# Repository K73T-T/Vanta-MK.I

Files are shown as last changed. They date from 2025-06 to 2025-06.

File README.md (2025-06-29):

# Vanta-MK.I
Vanta Mk.I is a custom, experimental 3D printer that uses a serial [SCARA](https://en.wikipedia.org/wiki/SCARA) arm for its motion system, instead of the more common Cartesian or CoreXY setups. It’s designed to explore uncommon 3D printing mechanics and share them through an open-source project.

# Project goals
- Capible of printing up to 600mm/s
- Print at 350mm/s reliably
- Easily serviceable
- full 24v electrical system
- V6 hotend
- Direct drive extruder
- Heated build plate
- Greater than 200x200x250 build volume
- stays togeter when tipped upside down

# Cad As of 6/26/25 



Onshape Document: https://cad.onshape.com/documents/15ec733589f1dfb19432007e/w/fc0f806dac7b21e964ade97e/e/b542b6b24f478e7f12932bdf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
440x440x722mm

|Hardware | | | | | |
|---|---|---|---|---|---|
| |PART |UNIT COST |QUANTITY|TOTAL |LINK |
| |150 Pieces M6 Screws Nuts Washers Set |$9.99 |1 |$9.99 |https://a.co/d/1KRJd6D |
| |GT2 Timing Belt Tensioner Torsion Spring |$1.63 |1 |$1.63 |https://www.aliexpress.us/item/2251832660949905.html? |
| |5 to 8 mm shaft coupling |$1.21 |2 |$2.42 |https://www.aliexpress.us/item/2251832618318567.html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 |
| |2m gt2 6mm width open loop belt |$5.54 |1 |$5.54 |https://www.aliexpress.us/item/3256805930504641.html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 |
| |Micro Limit Switch KW12-3 AC 250V 5A SPDT 1NO 1NC Micro Switch With Roller |$3.18 |1 |$3.18 |https://www.aliexpress.us/item/3256808277942672.html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 |
| |2040 extrusion 600mm |$0.00 |1 |$0.00 |Already owned |
| |2040 extrusion 400mm |$0.00 |1 |$0.00 |Already owned |
| |2020 extrusion 200mm |$0.00 |2 |$0.00 |Already owned |
| |2020 extrusion 180mm |$0.00 |6 |$0.00 |Already owned |
| |2020 extrusion 400mm |$0.00 |7 |$0.00 |Already owned |
| |2020 extrusion 550mm |$0.00 |4 |$0.00 |Already owned |
| |2020 extrusion 440mm |$0.00 |1 |$0.00 |Already owned |
| |2020 extrusion 360mm |$0.00 |4 |$0.00 |Already owned |
| |2PCS 350mm（13.78 Inches）Tr8x8 Lead Screw with T8 Brass Nut |$13.99 |1 |$13.99|https://a.co/d/b3srbob |
| |M3 countersunk screw set |$9.99 |1 |$9.99 |https://a.co/d/4OXnjIt |
| |Anycubic Kobra 3 Build plate assembly |$18.99 |1 |$18.99|https://a.co/d/51d8Cin |
| |m3 standoff set |$6.77 |1 |$6.77 |https://a.co/d/bvQ3HL7 |
| |24V 480W Switching Power Supply Adapter SMPS AC 110/220V to DC 24V |$30.99 |1 |$30.99|https://www.amazon.com/dp/B0CD1N3QH4?ref_=cm_sw_r_cp_ud_dp_ZGNP1G9RJW46EPHEQV2K_1 |
| |2Pcs 6mm x 400mm (0.236 x 15.74 inches) Vigorous Linear Motion Rods |$9.39 |2 |$18.78|https://a.co/d/gR9NUPh |
| |8Pcs LM6UU Linear Bearings |$8.81 |1 |$8.81 |https://a.co/d/9uNp9xQ |
| |2PCS Set GT2 Synchronous Wheel 20&36 Teeth 5mm Bore |$7.99 |1 |$7.99 |https://a.co/d/7NZQ2OG |
| |608zz ball bearing |$0.00 |7 |$0.00 |Already owned |
| |ruthex M3 Threaded Inserts Short - 100 Pieces RX-M3Sx4.0 Brass Heat Set Insert for Plastic Parts|$10.99 |1 |$10.99|https://a.co/d/din7U3K |
| |100x 304 Stainless Steel Balls 4mm |$2.60 |1 |$2.60 |https://www.aliexpress.us/item/3256808582039444.html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"order"%3A"104"%2C"eval"%3A"1"%7D&pdp_npi=4%40dis%21USD%211.89%211.79%21%21%211.89%211.79%21%402101c71a17490199564722814e3e99%2112000046585415385%21sea%21US%213447209169%21X&curPageLogUid=0d0BXeuBR6GZ&utparam-url=scene%3Asearch%7Cquery_from%3A&search_p4p_id=202506032352367638279615146210005463318_1 |
| |50x M3 x 30 Stainless Black 12.9 Grade Steel DIN912 Socket Cap Bolt |$4.17 |1 |$4.17 |https://www.aliexpress.us/item/3256802096694558.html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"order"%3A"159"%2C"eval"%3A"1"%7D&pdp_npi=4%40dis%21USD%213.34%213.14%21%21%213.34%213.14%21%402103277f17490198944277699e2b2a%2112000020718821802%21sea%21US%213447209169%21X&curPageLogUid=c3I1pqyON6dM&utparam-url=scene%3Asearch%7Cquery_from%3A |
| |Capricorn PTFE tube 1Meter |$0.00 |1 |$0.00 |Already owned |
| |PC4-M10 Pneumatic Fitting |$0.00 |1 |$0.00 |Already owned |
| |4KG LikeSilk PLA-F |$0.00 |4 |$0.00 |Already owned |
| |1KG CC3D TPU 72D |$0.00 |1 |$0.00 |Already owned |
| |4pack 3-Way End Corner Bracket Connector for T slot 2020 |$5.41 |1 |$5.41 |https://www.aliexpress.us/item/3256807720022867.html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,scm-url:1007.40050.354490.0,pvid:34e0b7f5-5c25-49d3-b820-5fca235ab151,tpp_buckets:668%232846%238109%231935&pdp_ext_f=%7B"order"%3A"154"%2C"eval"%3A"1"%2C"sceneId"%3A"30050"%7D&pdp_npi=4%40dis%21USD%215.41%215.40%21%21%215.41%215.40%21%402101c80017497905954292014e41a9%2112000042791422124%21rec%21US%213447209169%21X&utparam-url=scene%3ApcDetailBottomMoreOtherSeller%7Cquery_from%3A#nav-specification|
| |20Sets Corner Bracket 2020 |$6.17 |3 |$18.51|https://www.aliexpress.us/item/3256808845200216.html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,scm-url:1007.40050.354490.0,pvid:254cce5f-d16c-4065-86ea-1b569880f4e6,tpp_buckets:668%232846%238109%231935&pdp_ext_f=%7B"order"%3A"20"%2C"eval"%3A"1"%2C"sceneId"%3A"30050"%7D&pdp_npi=4%40dis%21USD%2116.12%218.06%21%21%21115.08%2157.54%21%402103246617497911398765399e43b3%2112000047649651210%21rec%21US%213447209169%21X&utparam-url=scene%3ApcDetailTopMoreOtherSeller%7Cquery_from%3A |
| |MGN12 Linear Rail Guide 400mm Linear Sliding Guideway with MGN12H |$17.07 |4 |$68.28|https://a.co/d/6MhZM3X |
| |6061 T651 Aluminum Sheet Metal 11 x 15 x 1/8 |$18.99 |1 |$18.99|https://a.co/d/2VpyzRv |
| |16 AWG Flexible Silicone Wire |$17.99 |1 |$17.99|https://a.co/d/c94o6UX |
| |50 M3 T nuts |$2.64 |1 |$2.64 |https://www.aliexpress.us/item/2251832628044342.html |
| |White Lithium Grease |$6.79 |1 |$6.79 |https://a.co/d/i3sqsRi |
| |E3D V6 Brass nozzle |$1.89 |2 |$3.78 |https://trianglelab.net/products/e3d-v6-brass-nozzle?VariantsId=10415 |
| |3D Printer Heatbed Leveling Kit Aluminum Hand Twist Leveling Nut + Springs |$8.07 |1 |$8.07 |https://www.aliexpress.us/item/3256803219034244.html? |
| |T8 Anti Backlash Spring Loaded Nut |$2.36 |1 |$2.36 |https://biqu.equipment/products/t8-anti-backlash-spring-loaded-nut-elimination-gap-nut-for-8mm-acme-threaded-rod-lead-screws-diy-cnc-3d-printer-parts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 |
| | | | | | |
|Electronics | | | | | |
| |PART |UNIT COST |QUANTITY|TOTAL |LINK |
| |trianglelab M8 inductive proximity sensor |$3.27 |1 |$3.27 |https://trianglelab.net/products/m8 |
| |Trianglelab 1.75 24V All-metal v6 hotend |$14.33 |1 |$14.33|https://trianglelab.net/products/v6-hotend-1?VariantsId=10946 |
| |Trianglelab 24V DDE V2 Orbiter 2.0 NO Hotend |$45.10 |1 |$45.10|https://trianglelab.net/products/dde-v2-orbiter-20-extruder?VariantsId=10328 |
| |BIQU Manta E3EZ V1.0+ 5pcs EZ2209 + TFT35SPI V2.1 (For CB1 V2.2) |$60.71 |1 |$60.71|https://biqu.equipment/products/bigtreetech-manta-e3ez-v1-0-for-ender3-ender3pro-ender5?variant=40214245081186 |
| |BIGTREETECH CB2 |$35.91 |1 |$35.91|https://biqu.equipment/products/bigtreetech-pi-2-cb2?variant=41018191839330 |
| |BiGTREETECH CB2 Heatsink |$5.58 |1 |$5.58 |https://biqu.equipment/products/bigtreetech-pi-2-cb2?variant=41283042213986 |
| |BIQU 15A 250V Rocker Switch Power |$5.10 |1 |$5.10 |https://biqu.equipment/products/biqu-15a-250v-rocker-switch-power-socket-inlet-module-plug-5a-fuse-switch-with-5pcs-16-14-awg-wiring-3-pin-iec320-c14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 |
| |STEPPERONLINE Nema 17 Stepper Motor 0.9deg 38mm 30Ncm 1.5A |$16.99 |2 |$33.98|https://www.aliexpress.us/item/3256805688801564.html? |
| |STEPPERONLINE Stepper Motor Nema 17 Bipolar 40mm 64oz.in(45Ncm) 2A |$9.75 |2 |$19.50|https://www.aliexpress.us/item/3256802068491329.html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 |
| |BIGTREETECH ADXL345/S2DW Accelerometer |$15.11 |1 |$15.11|https://biqu.equipment/products/adxl-345-accelerometer-board-for-36-stepper-motors?variant=40446852726882 |
| |BTT SFS V2.0 Smart Filament Sensor |$13.22 |1 |$13.22|https://biqu.equipment/products/btt-sfs-v2-0-smart-filament-sensor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 |
| | | | | | |
|Tools | | | | | |
| |PART |UNIT COST |QUANTITY|TOTAL |LINK |
| |1/6Pcs Tap Drill Bit Set Hex Shank |$4.86 |1 |$4.86 |https://www.aliexpress.us/item/3256805247501438.html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"order"%3A"484"%2C"eval"%3A"1"%7D&pdp_npi=4%40dis%21USD%211.91%211.91%21%21%2113.63%2113.63%21%402101effb17499397047086154ead90%2112000033059264633%21sea%21US%213447209169%21X&curPageLogUid=562tioNjmAle&utparam-url=scene%3Asearch%7Cquery_from%3A |
| |13pc Titanium Plated Drillbit set 1.5-6.5mm |$4.79 |1 |$4.79 |https://www.aliexpress.us/item/3256807544564003.html |
| |Heat Set Insert Soldering Iron Tip |$3.06 |1 |$3.06 |https://www.aliexpress.us/item/3256808012653406.html? |
| | | | | | |
| |Overall cost | | | | |
|Hardware |$309.65 | | | | |
|Electronics |$251.81 | | | | |
|Tools |$12.71 | | | | |
| | | | | | |
|Sum |$577.07 | | | | |
| | |Discount Code| | | |
|Aliexpress  |$136.26 |Huge20 |$114.17 | | |
|Amazon |$269.70 | | | | |
|Triangle lab|$73.13 | | | | |
|BIQU |$155.34 |GS8 |$146.82 | | |
| | | | | | |
|Total |$634.43 | |$603.89 | | |
|Budget Used |90.6% | |86.2% | | |

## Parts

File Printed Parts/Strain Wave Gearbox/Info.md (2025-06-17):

# License Notice for Modified Strain Wave Gearbox
Original design by [Unnecessary Automation](https://www.youtube.com/channel/UCuGbqmLhAL3zMx8-7ExxFag)
Published on Printables: [Strain Wave Gearbox](https://www.printables.com/model/1098371-strain-wave-gearbox)
Licensed under: [Creative Commons BY-NC-SA 4.0](https://creativecommons.org/licenses/by-nc-sa/4.0/legalcode)

# This license allows you to:

Share — copy and redistribute the material in any medium or format

Adapt — remix, transform, and build upon the material

# Under the following terms:

Attribution — You must give appropriate credit, provide a link to the license, and indicate if changes were made. You may do so in any reasonable manner, but not in any way that suggests the licensor endorses you or your use.

NonCommercial — You may not use the material for commercial purposes.

ShareAlike — If you remix, transform, or build upon the material, you must distribute your contributions under the same license.

# 🔧 Modifications I Made:
Redesigned the output shaft to resemble that of a standard NEMA 17 motor.

Made the shaft a separate part that threads into the output gear for horizontal printing to improved strength.

Adjusted the mounting pattern to match NEMA 17 hole spacing for direct compatibility with standard brackets.

Replaced the original threaded insert sizes with M3 headset inserts.

# Disclaimer:
I, the creator of the Vanta Mk.I project, am not endorsed by Unnecessary Automation or any entity affiliated with them. My modifications are shared in accordance with the terms of the CC BY-NC-SA 4.0 license.

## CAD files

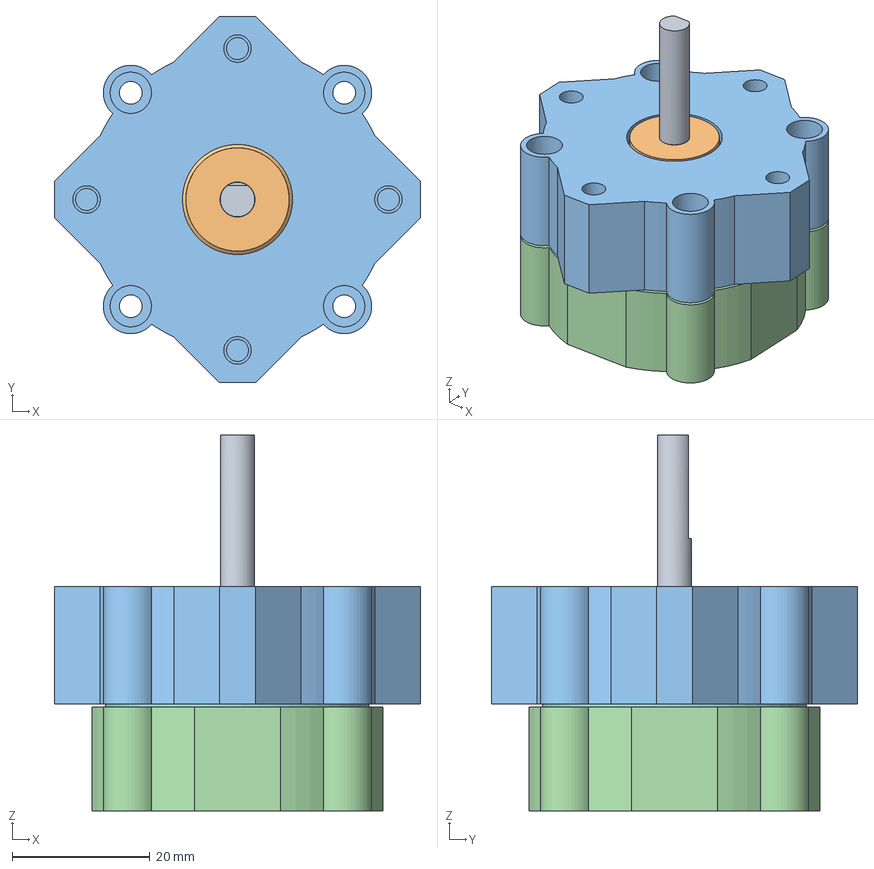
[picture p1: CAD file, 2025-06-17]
Printed Parts/Strain Wave Gearbox/gearbox full.step
53.2 x 53.2 x 54.6 mm

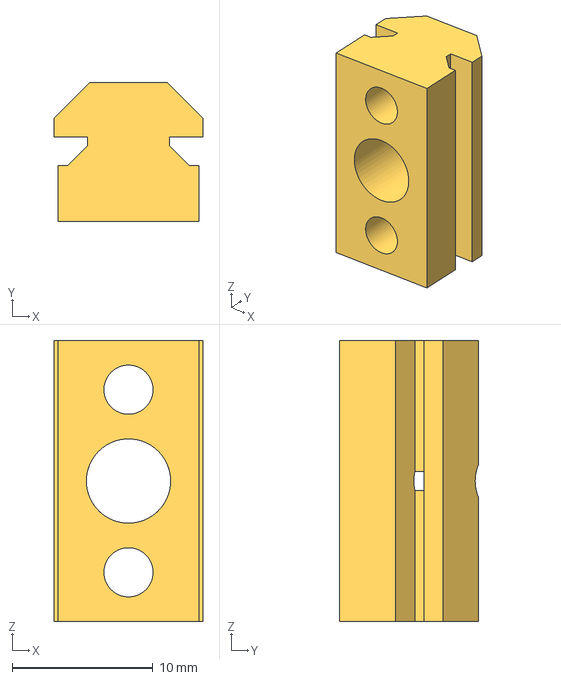
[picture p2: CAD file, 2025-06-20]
Printed Parts/4x Printed parts - Linear rod mount.step
10.6 x 9.90 x 20.0 mm

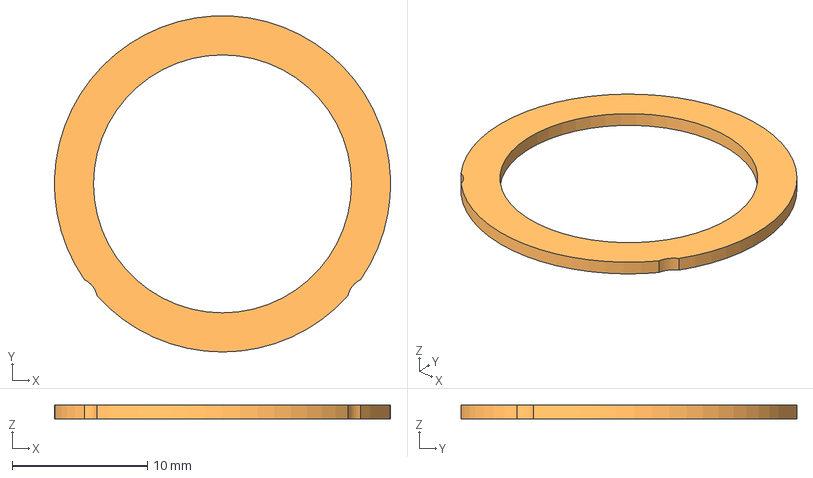
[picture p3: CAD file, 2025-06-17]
Printed Parts/Arms/bearing retainer for arm 2.step
24.9 x 24.9 x 1.00 mm

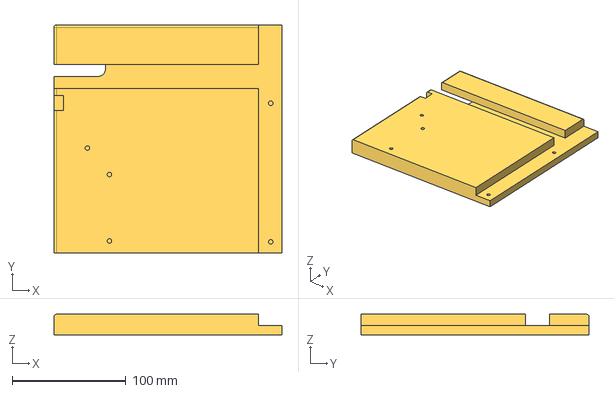
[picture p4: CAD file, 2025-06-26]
Printed Parts/Base/Printed parts - base FR.step
200.0 x 200.0 x 18.0 mm

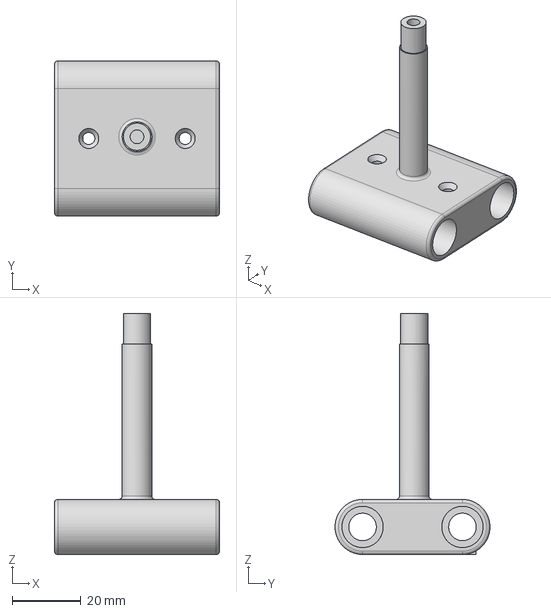
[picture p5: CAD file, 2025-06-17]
Printed Parts/Hotend Mount/Printed parts - Upper hotend mount.step
48.0 x 45.0 x 70.0 mm

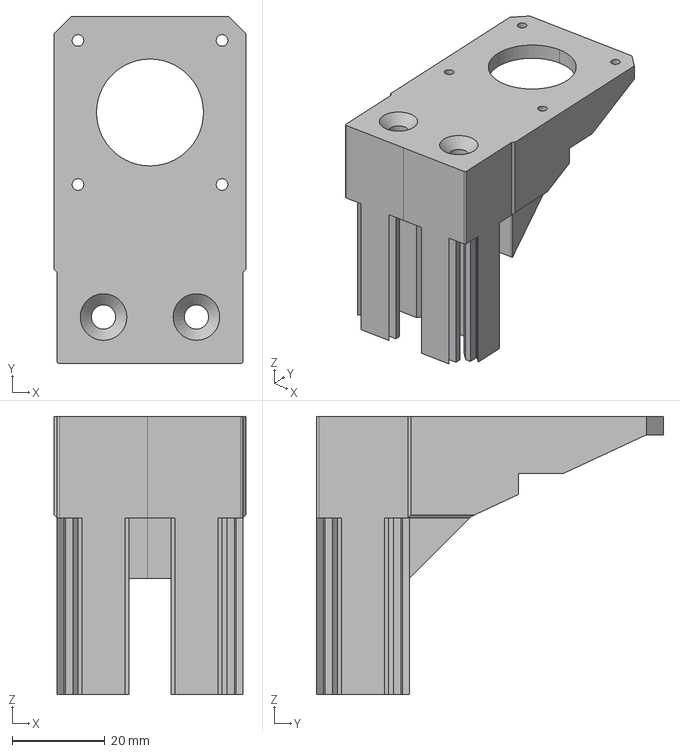
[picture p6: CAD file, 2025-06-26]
Printed Parts/Motor Mounts/Printed parts - motor mount 1.step
41.3 x 74.7 x 59.9 mm

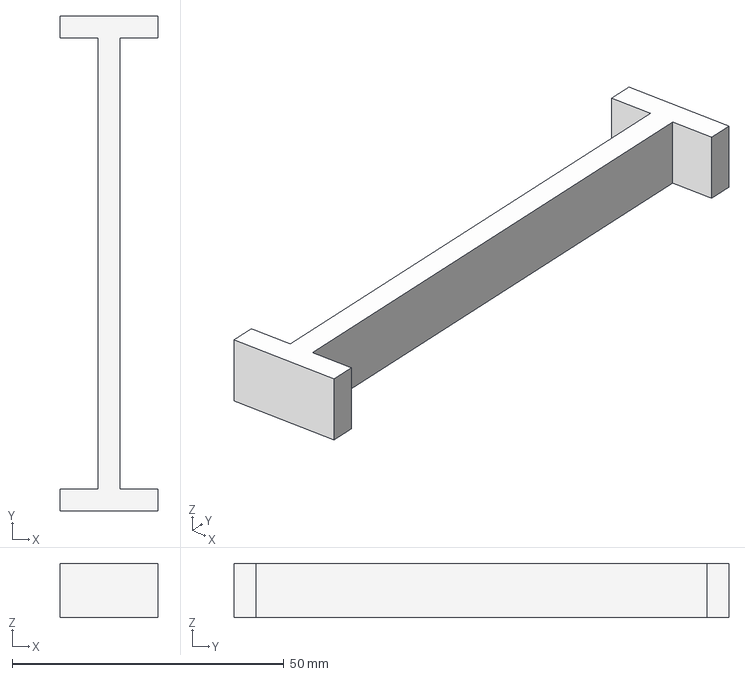
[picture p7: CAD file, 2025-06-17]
Printed Parts/Spool Roller/2x Spool Stand - connecting arm.step
18.0 x 91.0 x 10.0 mm

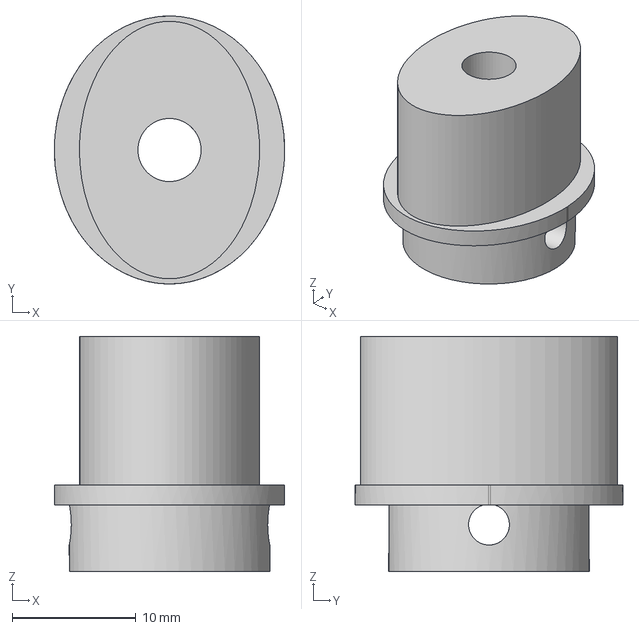
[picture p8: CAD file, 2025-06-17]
Printed Parts/Strain Wave Gearbox/Cam.step
18.6 x 21.6 x 19.0 mm

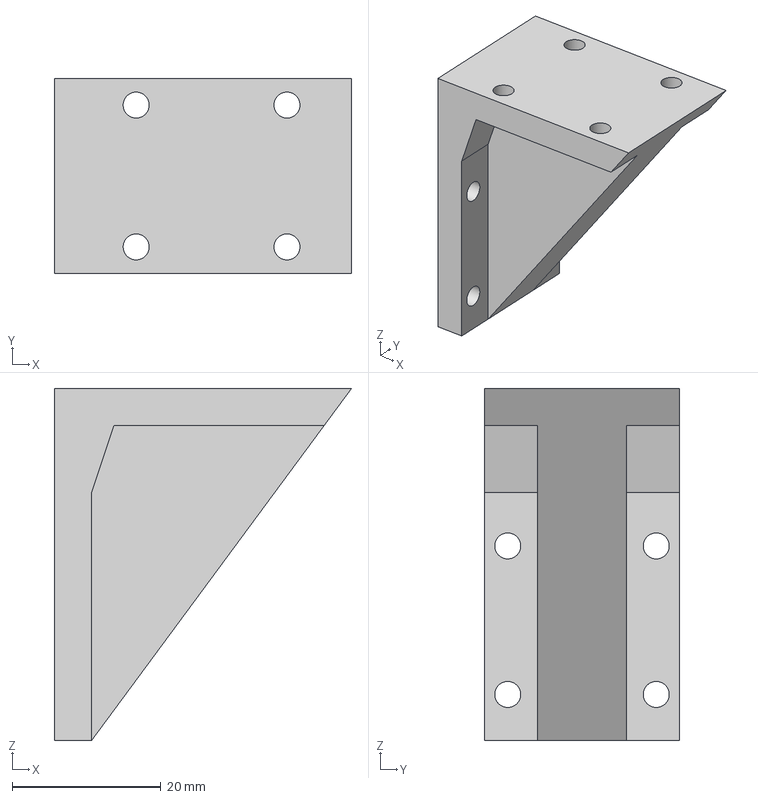
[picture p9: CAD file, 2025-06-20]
Printed Parts/4x Printed parts - Build plate mount Bracket.step
40.0 x 26.2 x 47.4 mm

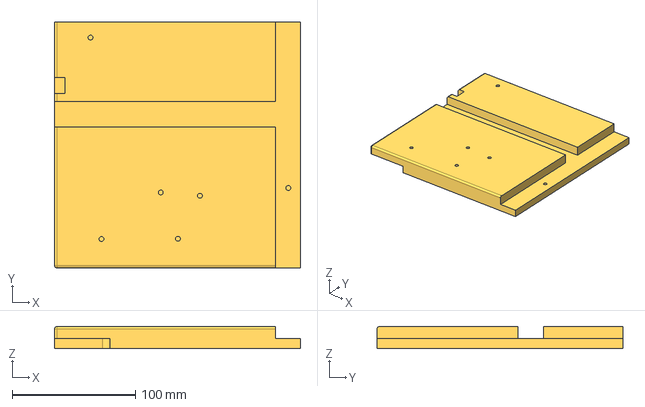
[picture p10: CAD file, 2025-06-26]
Printed Parts/Base/Printed parts - base RR.step
200.0 x 200.0 x 18.0 mm

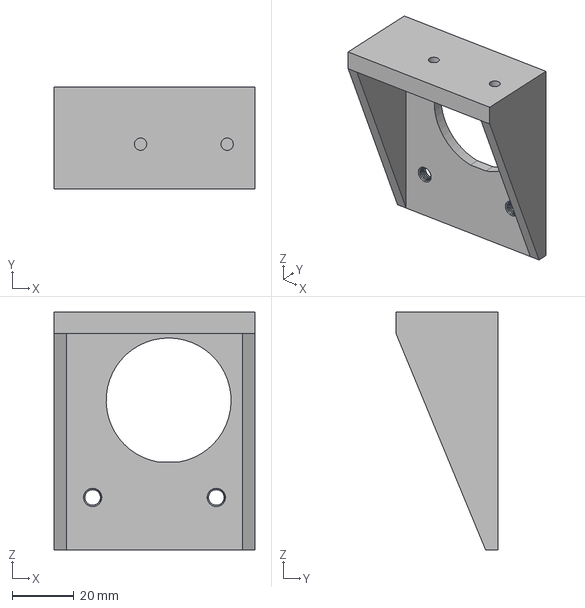
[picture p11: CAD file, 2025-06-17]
Printed Parts/Hotend Mount/Printed parts - Lower hotend mount.step
65.0 x 33.0 x 77.0 mm

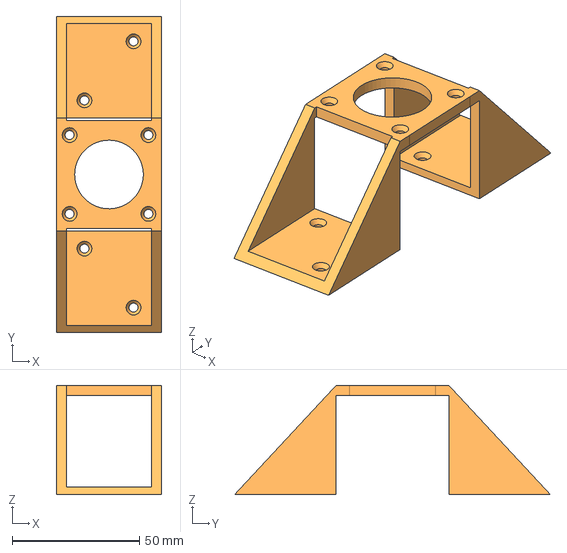
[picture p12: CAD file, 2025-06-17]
Printed Parts/Motor Mounts/Printed parts - Z motor mount Left (mirrored).step
41.3 x 124.3 x 43.0 mm

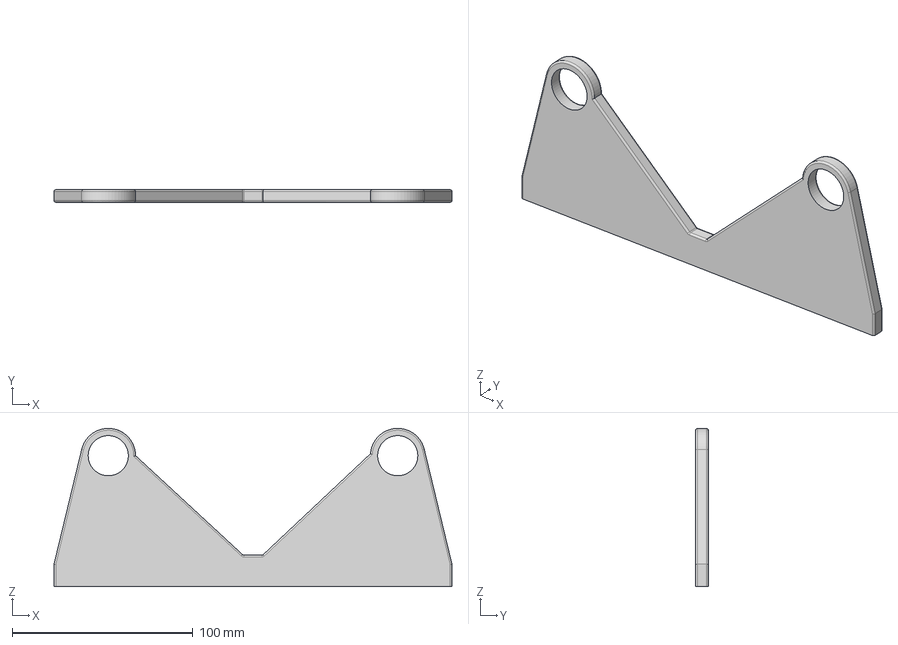
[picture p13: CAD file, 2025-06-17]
Printed Parts/Spool Roller/2x Spool Stand - wall.step
220.0 x 7.00 x 87.5 mm

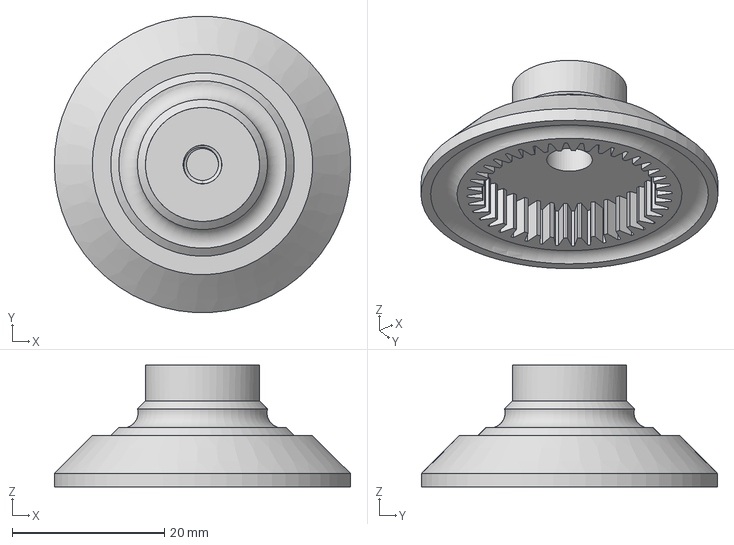
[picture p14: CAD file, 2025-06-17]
Printed Parts/Strain Wave Gearbox/Output gear.step
39.0 x 38.9 x 16.0 mm

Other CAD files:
Printed Parts/2x Printed parts - Linear bearing holder.step
Printed Parts/Base/Printed parts - base FL.step
Printed Parts/Hotend Mount/Printed parts - Upper hotend mount retainer.step
Printed Parts/Motor Mounts/Printed parts - Motor 2 Mount.step
Printed Parts/4x vslot_joiner.step
Printed Parts/Arms/Printed parts - Arm 1 bolt.step
Printed Parts/Arms/Printed parts - Arm 2 Bolt.step
Printed Parts/Arms/Printed parts - Arm 2 Top.step
Printed Parts/Arms/Printed parts - Arm 2 bottom.step
Printed Parts/Arms/Printed parts - Bearing insert for bearing holder and arm 1 bolt.step
Printed Parts/Arms/Printed parts - arm 1.step
Printed Parts/Base/4x 3d printer foot.step
Printed Parts/Base/4x Printed parts - Foot Plate.step
Printed Parts/Base/Printed parts - base RL.step
Printed Parts/Motor Mounts/2x motor shaft spacer.step
Printed Parts/Motor Mounts/Printed parts - Bearing mount.step
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

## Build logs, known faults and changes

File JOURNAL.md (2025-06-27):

# Vanta Mk.I by Joshua aka Controw_
Created 5/20/25

~ 70 hours

## 5/24/25 Start cad and deciding on components 
 11:04am - 9:48pm 10 hours and 44 minutes 
 
 ### Control Board
- I chose the BTT Manta E3EZ as the main controller board since setup is straightforward, and the fact that it allows the installation of a compute module that supports use of Klipper as the printing software (which I want to use.) Thankfully, it includes native support for dual Z motors- good for improving bed leveling precision in this build. I considered other boards, but the E3EZ's plug-and-play layout and expandability made it a preferable fit. Looking forward to testing its CAN bus support down the line if I add toolhead mods
  
 

### Motors
- For the motors, I chose the StepperOnline NEMA 17 stepper motors with 0.9° step angle. High-resolution movement ensures accurate articulation and positioning. Chose standard NEMA 17 motors with 1.8° step angle for the Z-axis since precision is less critical there and for less cost

### Extruder
- For the extruder, I chose the Orbiter V2 kit from Triangle-lab (Direct Drive). It has high torque and a compact form, and offers reliable filament control for rather precise printing, especially with flexible or exotic materials. Lightweight planetary gear system minimizes strain on the carriage while maintaining performance



### Build Plate
- For the build plate, I chose the Anycubic Kobra 3 Build Plate Assembly. Wanted to use an off-the-shelf build plate assembly from an existing printer model to reduce complexity and cost, and I can cut off time from the construction of the full assembly. After comparing several options online, I chose the Kobra 3 plate since I’m happy with the size, cost, and since it's heated

## 5/25/25 Work on cad again and finalizing components

### Z Axis Configuration
- Went with 2 independent Z motors for stability, even motion, and dual Z gives the ability to shift the build plate ever so slightly for tramming

### XY Gantry
- For the XY gantry, I went for linear rods because they are easy, inexpensive, and reliable

### PSU
- For the PSU I went with a basic 24V 20A 480W Because of its versatility

 12:37PM to 3:12AM 14 hours 35 minutes 

cad at end of day 2

 

## Start of day 3 5/26/25 working on cad a bit more
 12:52 PM - 5:36 PM 4 hours 44 minutes
- Got the general place for the z axis motors and lead screws 
- Mounted rails to motion arm

Cad at end of day 3 



## Start of Day 4 5/27/25 Making a parts list and mounting second SCARA motor
9:34 PM - 11:42 PM 3 hours 8 minutes

[Parts List](https://github.com/K73T-T/Vanta-MK.I/blob/main/Parts%20list.md)

Mounted second motor 



## Day 5 5/28/25 
8:46 PM - 11:12 PM

Adjusted clearence for first motor mount so the belt does not clip into it

clip no yes

[Found wiring diagram for BIQU Manta e3ez](https://os.ratrig.com/docs/boards/btt/manta-e3ez/) [another one](https://cdn.shopify.com/s/files/1/1619/4791/files/E3EZ_1200x.png?v=1700039972)

Mounted the control board (14 minutes)



Mounted PSU (46 minutes)

Added mount for power switch (33 Minutes)



Finalized z axis motor positions, will make mounts tomorrow
 
Cad at end of day 5



## Day 6 5/30/25 

Made A bill of materials
4:36 PM - 7:02 PM 

## Day 7 5/31/25 More cad

Mounted both z axis motors - 46 Minutes



Moved control board for better accessibility - 13 minutes



I realized that the second arm was not possible to cnc so i optimized it for subtractive manufacturing - 1 hour 33 minutes



after making a mount for the extruder and hot end it removed over 100mm of usable z aixs build volume so i made the disicion to increase the hight of the printer by 100m by changing the 2020 extrusions from 500 to 600 mm and the 10x450 mm rods to 10x550mm rods - 11:35 PM - 1:59 AM 2 hours 24 minutes





made feet for the bottem of the printer 47 minutes

I modeled them after the feet for the Anycubic kobra 2 Neo because I already have a set of them since I swaped them out for taller ones on my kobra 2 neo



## Day 8 6/3/25 

Worked out the resolution of the printer was ~0.21 mm and i was dissatisfied with this so i did some research and found [this video by Unnecessary Automation on youtube](https://www.youtube.com/watch?v=52_t2FcqHOs) of them making a strain wave gearbox to increse the resolution of a nema 17 stepper motor and found that they published the files on [printables](https://www.printables.com/model/1098371-strain-wave-gearbox/files) so i modified them a bit to work better for my application, and found that after the addition of this gearbox it greatly improved the resolution from ~0.21mm to ~10-20 microns (0.01 - 0.02 mm) without microstepping and with a microstep of 1/2 it brings the resolution down to sub 10 micron accuracy which is much much better than before (~21x better) with the only real downside being the theoretical speed of the printer will be greatly lowered (time spent ~ 2 hours)



## Day 9 6/4/25 

Made a simple external spool roller (45 Minutes)



Added a PTFE tube mounting point to for a PTFE tube to go from the frame to the extruder (22 Minutes)



## Day 10 6/8/25

Made use of the extra 200mm of 2020 extursion by adding a support to the front two frame rods (23 Minutes)



Added suport arms to the rear 2 frame rods (34 minutes)



Mounted limit switches (20 minutes)




Lightend the build plate mount (30 minutes)



## Day 11 6/11/25

After some feedback I have decied to change the frame to use 2020 extrusions instead of the 10mm rods to increase stabity  (2 Hours)



## Day 12 6/12/25

Added two more 2020 extrusions to the top and moved the PTFE tube fitting (30 minutes)



## Day 13 6/13/25

Added linear rails for the build plate to make it more stable (1.5 hours)



## Day 14 6/16/25

Moved limit swtiches because the way they were before would not work for a SCARA system (25 Minutes)



## Day 15 6/26/25 

Found that my FRC Team had quite a few 2020 and 2040 extrusions that they had no use for so I was able to use them for my printer instead of having to buy them, which saved me over $80.



Started cutting out 2020 extrusions and will cut the rest on Monday (30 mintues)


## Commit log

2025-05-31 Update Vanta Mk.I BOM.csv
    [Vanta Mk.I BOM.csv]
2025-06-17 Create Printed parts - base RR.step
    [Printed parts - base RR.step]
2025-06-17 Rename Printed parts - base RR.step to SS
2025-06-17 Create Strain Wave Gearbox
2025-06-22 Rename gearbox parts.step to gearbox full.step
    [gearbox full.step]
